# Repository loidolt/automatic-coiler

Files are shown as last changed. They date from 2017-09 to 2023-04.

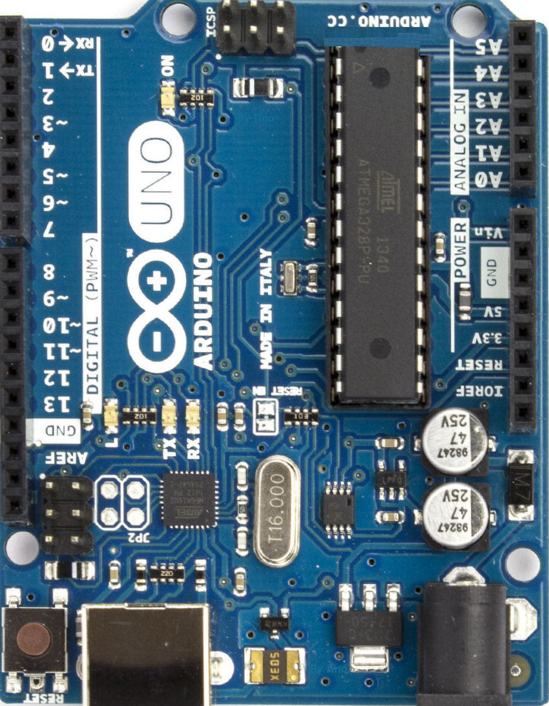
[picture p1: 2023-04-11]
V1/3d-model/AutomaticCoiler/ArduinoRev3CaraComponentes.jpg

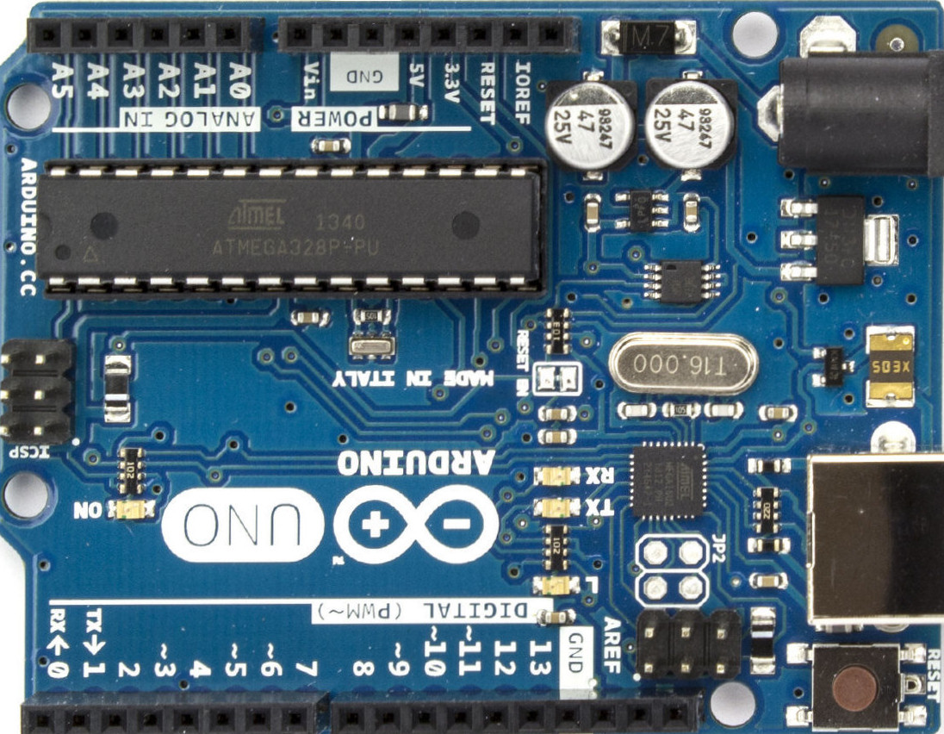
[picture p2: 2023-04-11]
V1/3d-model/AutomaticCoiler/CaraComponentes2.jpg

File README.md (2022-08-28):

---
published: true
status: complete
date: 10/26/2016
tags: 3DPrinting Electronics
description: An automatic winding machine for coiling up small cords, strings or wire.
slug: automatic-winding-machine
---

# Automatic Coiler

An automatic winding machine for coiling up small cords, strings or wire.

## Table of Contents

- [Automatic Coiler](#automatic-coiler)
  - [Table of Contents](#table-of-contents)
  - [Summary](#summary)
  - [Print Settings](#print-settings)
    - [Resolution:](#resolution)
    - [Infill:](#infill)
    - [Filament_material:](#filament_material)
    - [Notes:](#notes)
  - [Bill of Materials](#bill-of-materials)
    - [Hardware](#hardware)
      - [Tubing and Shafts:](#tubing-and-shafts)
      - [Bearings:](#bearings)
      - [Fasteners:](#fasteners)
      - [Other:](#other)
    - [Electronics](#electronics)
      - [Mechanical:](#mechanical)
      - [Control:](#control)

## Summary

This is an automatic winding machine for coiling up small cords, strings, or wires. We needed a way to reliably coil up specific lengths of cord for sale in a kit. This machine is the updated version of my original Automatic Winding Machine, making it more reliable, easier to use, and above all much, much quieter.

The rotary encoder keeps track of the distance coiled with a closed-loop system. This allows more foolproof operation, recovery if the spool hangs up or jams, and the ability to adjust the diameter of the coil without having to change the code.

This version features an LCD display with button controls, easy to edit firmware, more robust encoder guide system, an integrated spool holder, a quiet belt-driven platter, enclosed electronics, and a ton of other tiny tweaks and improvements.

Let me know if you have any questions or need build instructions. I'm happy to provide more detail but will need time to do the full instructional write-up. I can also provide pre-built custom acrylic panels and aluminum plates on request for a small fee.

Happy building!

## Print Settings

### Resolution:

.3

### Infill:

50

### Filament_material:

PLA or PETG

### Notes:

Print the Guide Wheels and Idler Wheel at high resolution, I used 0.1 mm layer height and 3 perimeters.

Print the Plate Shaft Mount solid (100% infill) to ensure it is nice and rigid.

## Bill of Materials

### Hardware

2020 Misumi T-Slot:

- 16x 260mm
- 4x 450mm

Lots of Cast Aluminum Corner Brackets (or print some if you want plastic brackets)

#### Tubing and Shafts:

- 1x 8mm x 75mm Round Metal Rod
- 2x 16mm OD x 215mm Round Aluminum Tube

#### Bearings:

18x 623Z Flange Bearing
2x 608Z

#### Fasteners:

- 4x M8-1.25 x 16mm Button Head Hex Socket Cap Screws
- A bunch of M4 screws, washers, and t-slot nuts

#### Other:

- M3 x 50mm Round Aluminum Standoff
- 1/4" x 12" Aluminum 5052 Plate Disk
- 2x 12"x12" White Acrylic Sheet

### Electronics

#### Mechanical:

- 1x Signswise 600p/r Incremental Rotary Encoder Dc5-24v Wide Voltage Power Supply 6mm Shaft
- 1x Greartisan DC 12V 200RPM Gear Motor High Torque
- 1x GT2 Pulley 20 Teeth 6mm Bore
- 1x GT2 Pulley 60 Teeth 8mm Bore
- 1x GT2 158mm Timing Belt Closed Loop
- 1x 10A 250V AC Inlet with Rocker Switch
- 1x Panel Mount USB Cable B to B

#### Control:

- 1x L298N Motor Drive
- 1x Arduino Nano
- 1x 16x2 LCD
- 2x 40mm Fan
- 1x 120v to 12v Power Supply (5-10 amp depending on your motor choice)
- 4x Arcade Buttons

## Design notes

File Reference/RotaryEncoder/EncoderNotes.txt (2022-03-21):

Encoders have an A and a B output. Tieing A to and interrupt pin and B to an input. On interrupt from A check B and if HIGH add 1 to PositionVar, if B is low Subtract 1 from PositionVar.

https://youtu.be/dTGITLnYAY0

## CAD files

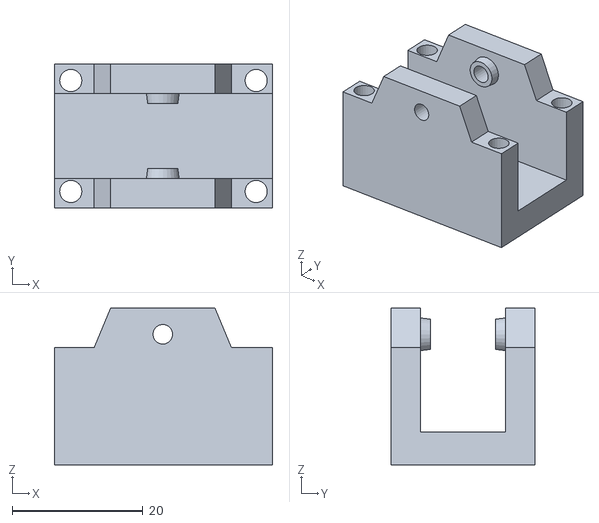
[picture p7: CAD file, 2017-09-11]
V1/stl/Encoder/EncoderIdlerAssembly.stl
33.4 x 22.0 x 24.0

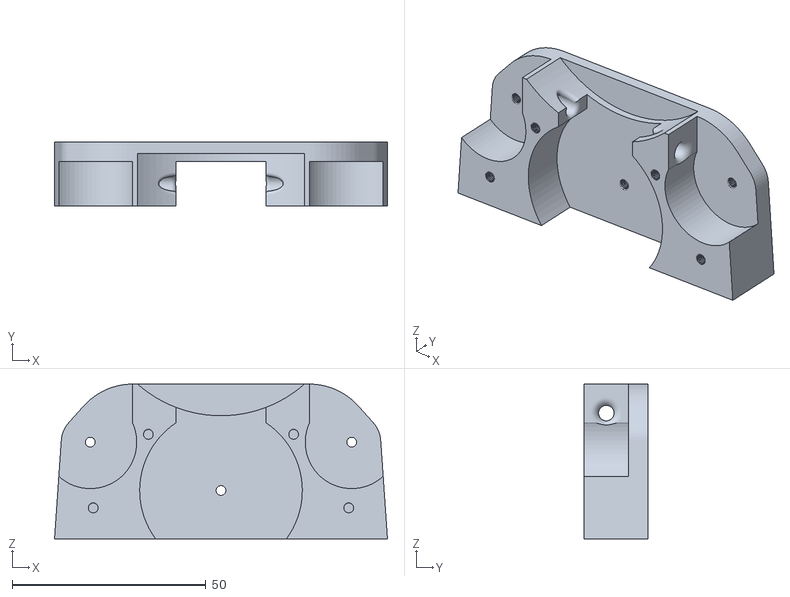
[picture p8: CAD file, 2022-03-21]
3d-model/stl/EncoderCordGuideMain.stl
86.0 x 16.5 x 40.0

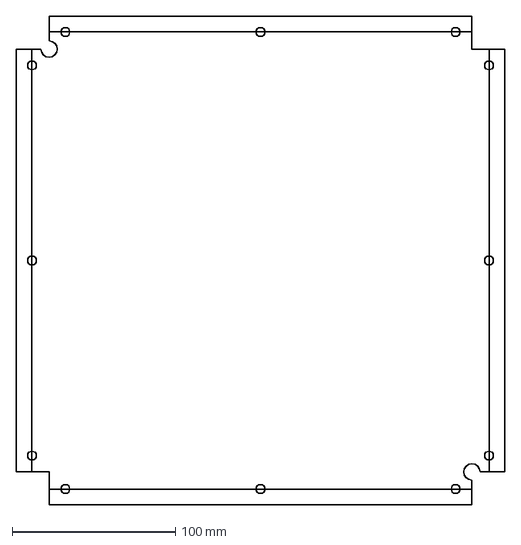
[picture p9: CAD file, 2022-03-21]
3d-model/ElectronicsCover.dxf
299.0 x 299.0 mm

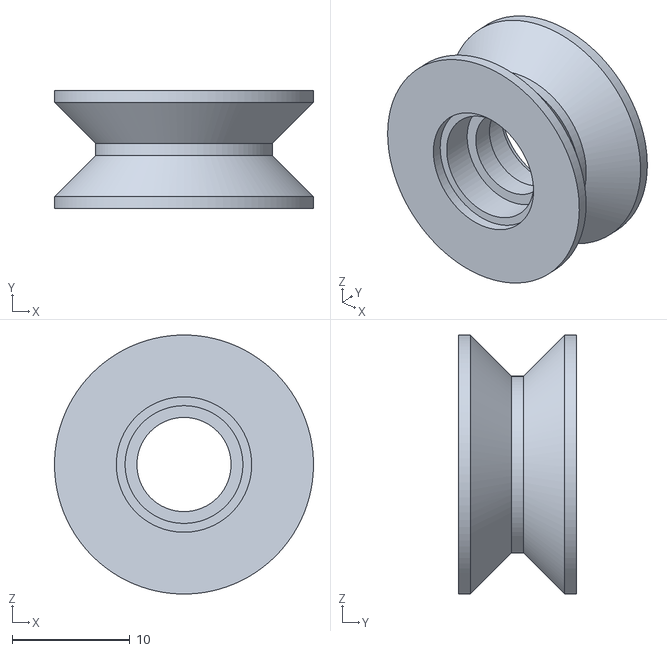
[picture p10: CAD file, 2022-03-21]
3d-model/stl/CordWheel.stl
22.0 x 10.0 x 22.0

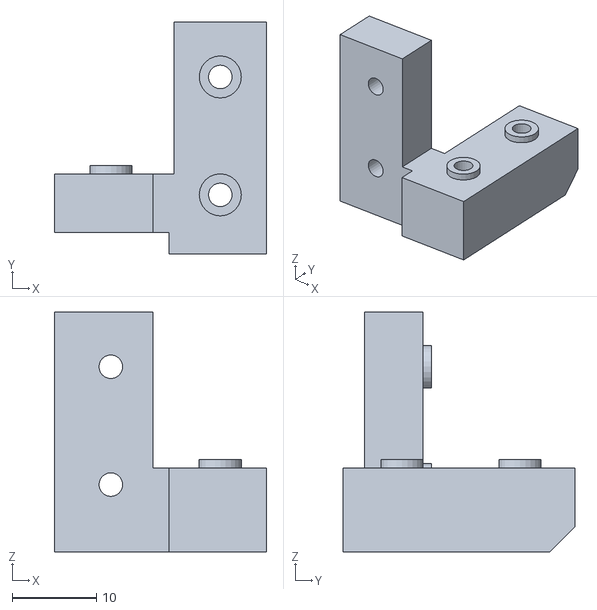
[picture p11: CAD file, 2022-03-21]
3d-model/stl/V2/CordGuideBearings.stl
25.2 x 27.5 x 28.5

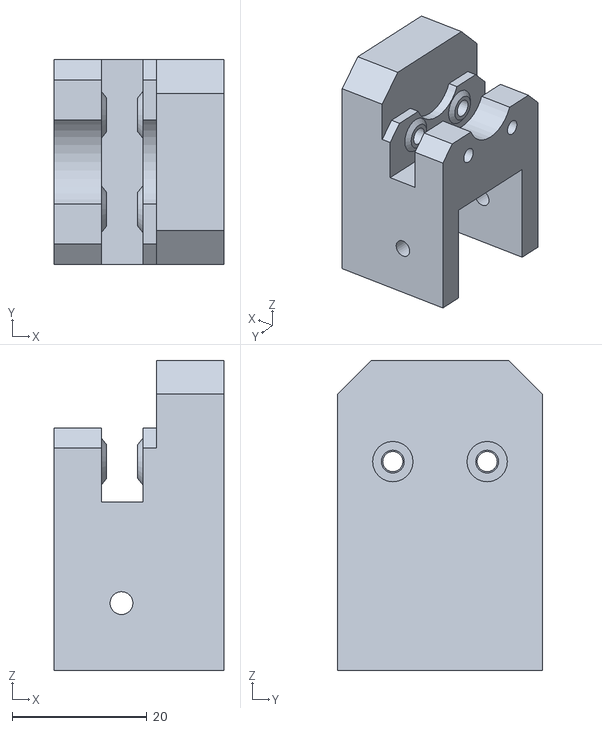
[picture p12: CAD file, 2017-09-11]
V1/3d-model/SpoolHolder/stl/BearingMount.stl
25.2 x 30.4 x 46.0

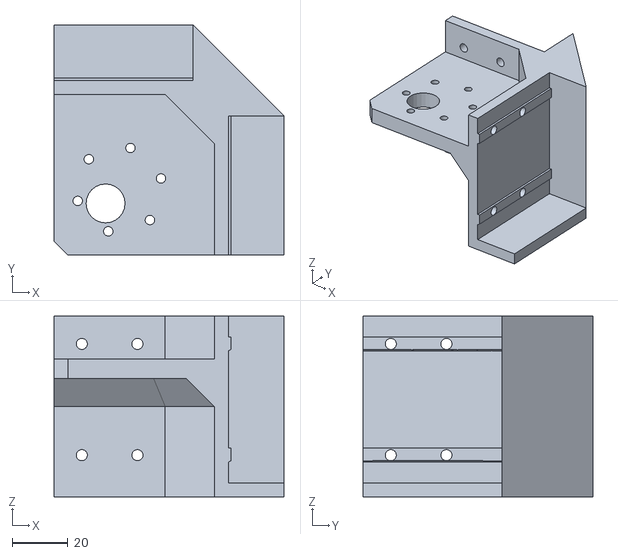
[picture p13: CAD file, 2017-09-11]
V1/stl/DCMotorCorner.stl
82.7 x 82.7 x 65.0

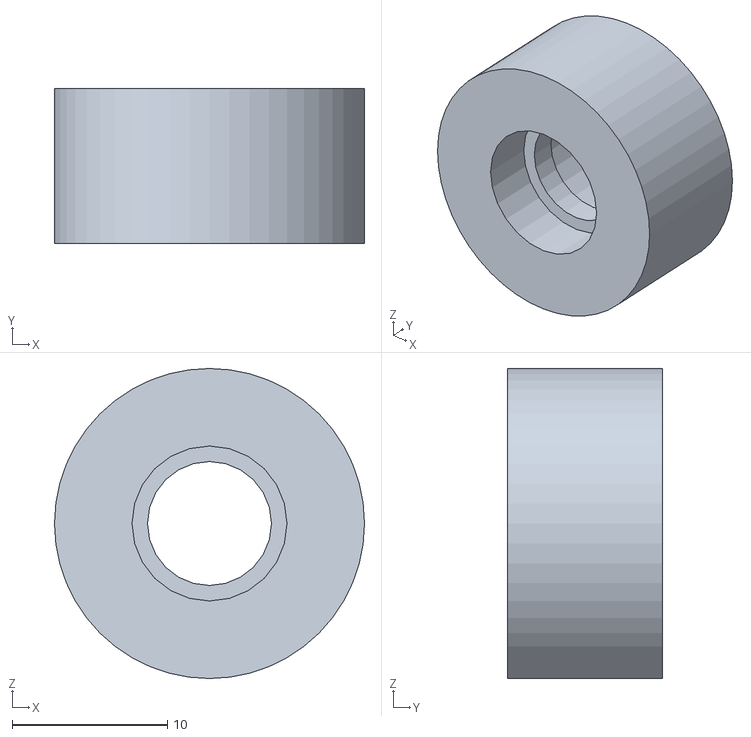
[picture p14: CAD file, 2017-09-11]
V1/stl/Encoder/IdlerWheel.stl
20.0 x 10.0 x 20.0

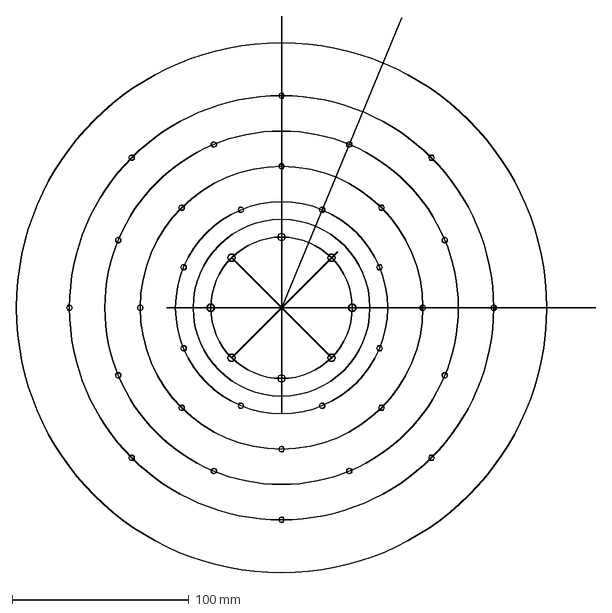
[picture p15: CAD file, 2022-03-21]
3d-model/PlateHolePattern.dxf
327.7 x 315.0 mm

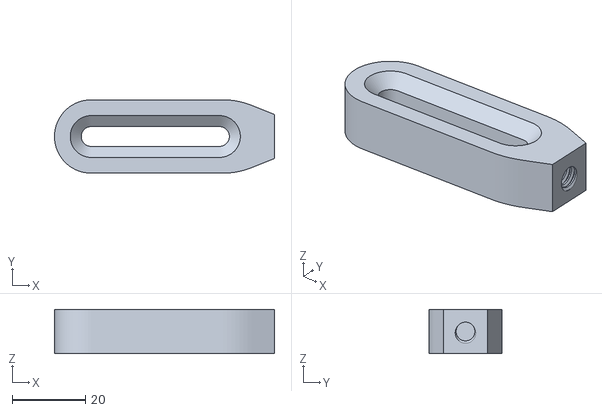
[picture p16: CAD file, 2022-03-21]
3d-model/stl/CenteringGuideArm.stl
60.0 x 20.0 x 12.0

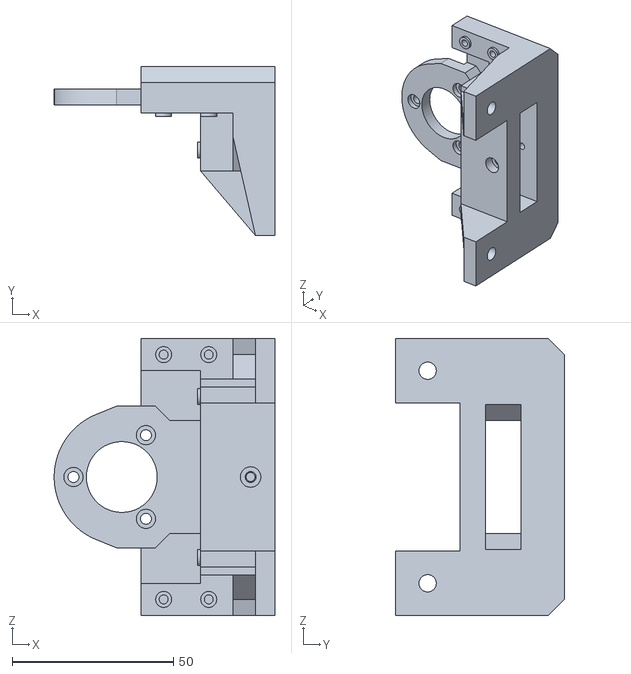
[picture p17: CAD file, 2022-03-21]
3d-model/stl/V2/EncoderHousing.stl
68.5 x 52.5 x 86.0

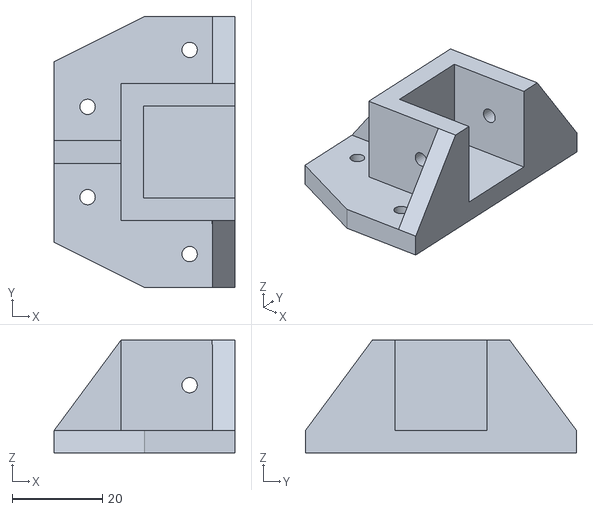
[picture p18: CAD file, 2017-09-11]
V1/3d-model/SpoolHolder/stl/90DegreeBracket.stl
40.0 x 60.0 x 25.0

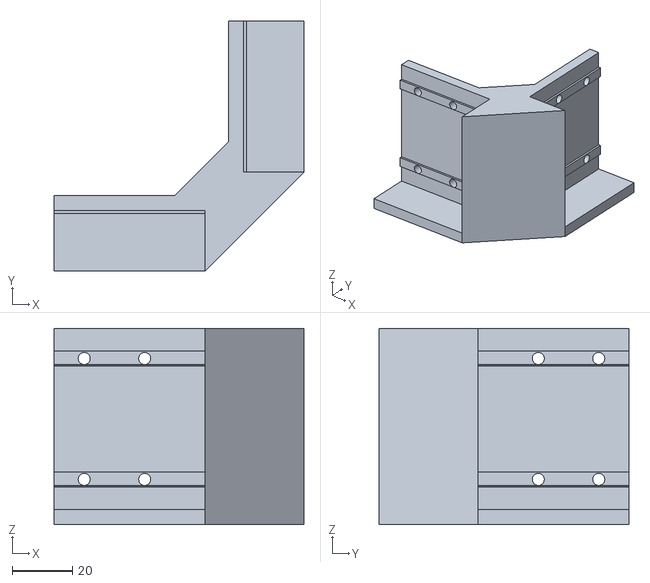
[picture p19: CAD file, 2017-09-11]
V1/stl/Corner.stl
82.7 x 82.7 x 65.0

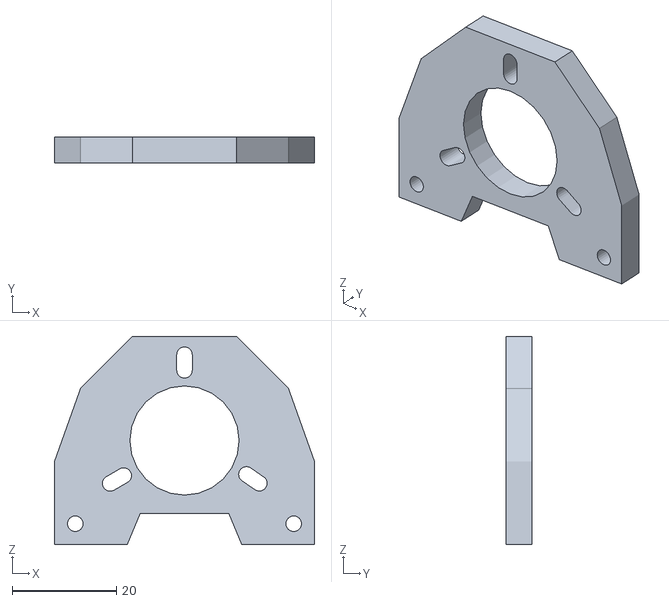
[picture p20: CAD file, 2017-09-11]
V1/stl/Encoder/EncoderMountPlate.stl
50.0 x 5.00 x 40.0

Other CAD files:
3d-model/stl/SidePanelACOutlet.stl
3d-model/stl/V2/SidePanelFan.stl
V1/3d-model/SpoolHolder/stl/Foot.stl
V1/stl/Encoder/EncoderHousing.stl
3d-model/stl/BearingBlock.stl
3d-model/stl/CenteringGuideMount.stl
3d-model/stl/ControlPanelLeft.stl
3d-model/stl/ControlPanelRight.stl
3d-model/stl/EncoderCordGuideCover.stl
3d-model/stl/GuideMount.stl
3d-model/stl/GuideWheelHolder.stl
3d-model/stl/GuideWheelHolderClamp.stl
3d-model/stl/IdlerWheel.stl
3d-model/stl/L298NMount.stl
3d-model/stl/MotorMount.stl
3d-model/stl/PCBMount.stl
3d-model/stl/PlateShaftMount.stl
3d-model/stl/RodHolderLeft.stl
3d-model/stl/RodHolderRight.stl
3d-model/stl/SidePanel.stl
3d-model/stl/SidePanelFan.stl
3d-model/stl/SidePanelVent.stl
3d-model/stl/SpoolHolder.stl
3d-model/stl/USBPanel.stl
3d-model/stl/V1.5/BearingToTubeCoupler.stl
3d-model/stl/V1.5/CordGuide.stl
3d-model/stl/V1.5/GuideClamp.stl
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

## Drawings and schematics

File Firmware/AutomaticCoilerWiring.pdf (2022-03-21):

## VCC VCC

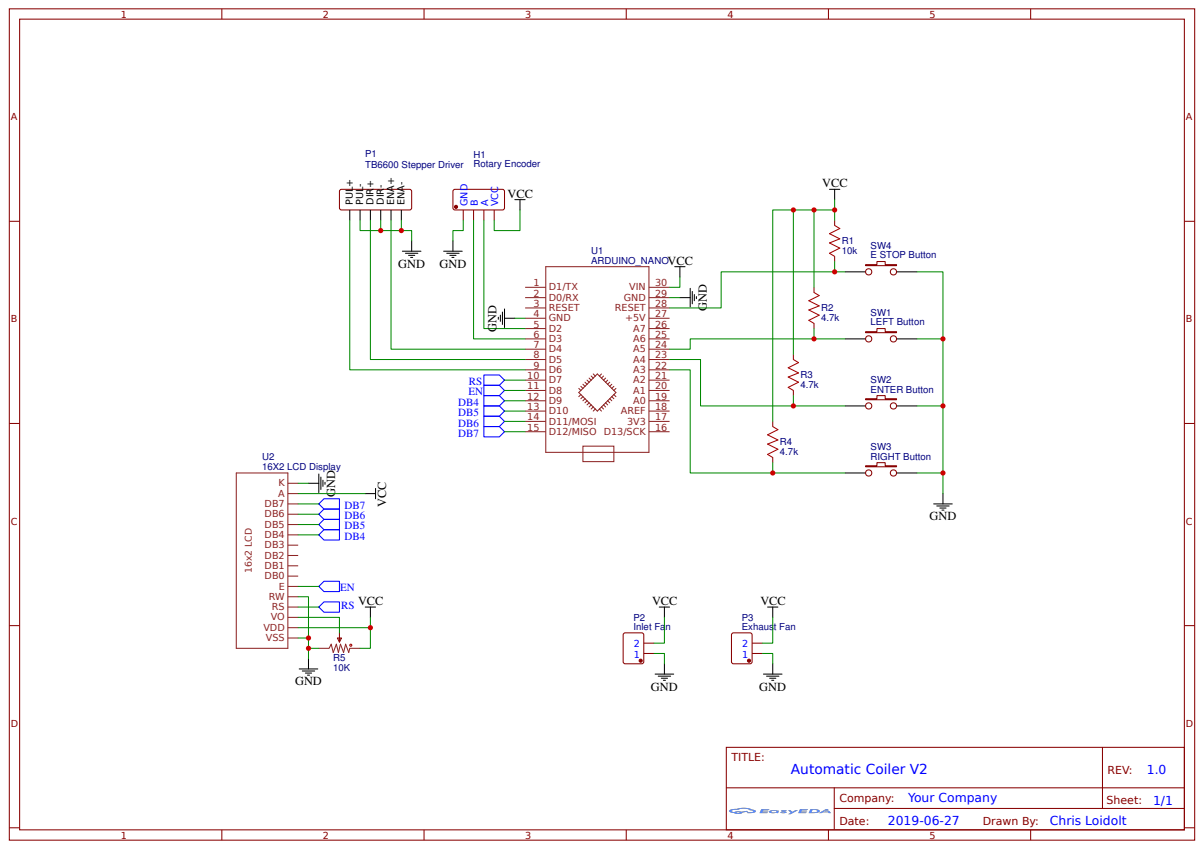
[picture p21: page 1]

Drawn By: Chris Loidolt

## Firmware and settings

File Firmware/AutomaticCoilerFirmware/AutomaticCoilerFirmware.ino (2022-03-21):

//Automatic Coiler V3
//Chris Loidolt
//03/15/2022

#include <LiquidCrystal.h>

//LCD
LiquidCrystal lcd(7, 8, 9, 10, 11, 12);
unsigned long previousMillis = 0; // will store last time LCD was updated
const long updateInterval = 200; // interval at which to update LCD while running job (milliseconds)

//Define Various Menu Variables used throughout
int timer = 0;
byte totalRows = 2;              // total rows of LCD
byte totalCols = 16;             // total columns of LCD
int returndata = 0;              // Used for return of button presses
unsigned long timeoutTime = 0;   // this is set and compared to millis to see when the user last did something.
const int menuTimeout = 20000;   // time to timeout in a menu when user doesn't do anything.
unsigned long lastButtonPressed; // this is when the last button was pressed. It's used to debounce.
const int debounceTime = 150;    // this is the debounce and hold delay. Otherwise, you will FLY through the menu by touching the button.

const int buttonUp = A5;     // Set pin for UP Button
const int buttonSelect = A4; // Set pin for SLELECT Button
const int buttonDown = A3;   // Set pin for DOWN Button

int buttonStateUp = 0; // Initalise ButtonStates
int buttonStateDown = 0;
int buttonState;

// constants for indicating whether cursor should be redrawn
#define MOVECURSOR 1
// constants for indicating whether cursor should be redrawn
#define MOVELIST 2

//Encoder
const int encoder_a = 2; // Green (Red - 5v, Black - GND)
const int encoder_b = 3; // White
long encoder = 0;
const float wheelPerimeter = 200; //mm
const int pulsesPerRev = 200;
float distancePerPulse;

//L298N Motor Driver
#define enA 6
#define in1 5
#define in2 4
int speedPWM = 0;
int minPWM = 120;

bool CWRotation = true;
int acceleration = 2;

//Job Variables
float feedLength = 0;
float distance = 0;
float overshootLength = 260; //Deceleration overshoot length offset

//Menu Variables
int menuItem = 0;

//Function Prototypes
void encoderPinChangeA(void);
void encoderPinChangeB(void);
int read_buttons();
void RunJob(void);
void calcDistance();
void EnterQty(void);

//Preset Lengths (inches)
const int guylineCordLength = 1200;
const int ridgelineLength = 300;

void setup()
{

  // set up the LCD's number of columns and rows:
  lcd.begin(totalCols, totalRows);

  // initialize the serial communications port:
  Serial.begin(9600);

  pinMode(buttonUp, INPUT);
  pinMode(buttonDown, INPUT);
  pinMode(buttonSelect, INPUT);

  // Encoder Setup
  pinMode(encoder_a, INPUT_PULLUP);
  pinMode(encoder_b, INPUT_PULLUP);
  
  attachInterrupt(0, encoderPinChangeA, RISING);
  
  //Calculate encoder distance per pulse
  distancePerPulse = wheelPerimeter / pulsesPerRev;

  //Motor Setup
  pinMode(enA, OUTPUT);
  pinMode(in1, OUTPUT);
  pinMode(in2, OUTPUT);
  // Set initial rotation direction
  digitalWrite(in1, LOW);
  digitalWrite(in2, HIGH);

  speedPWM = minPWM;

  // Boot Up Message
  Serial.println("Automatic Coiler");
  lcd.print("Automatic Coiler");
  lcd.setCursor(0, 1);
  lcd.print("Starting Up");
  Serial.print("Starting Up");
  delay(300);
  for (int i = 0; i < 6; i++)
  {
    Serial.print(".");
    lcd.print(".");
    delay(100);
  }

  Serial.begin(9600);

  lcd.clear();

  displayMenu();
}

void calcDistance()
{
  //Convert mm to inches
  distance = (encoder * distancePerPulse) / 25.4;
  Serial.println(distance);
}

void RunJob(int feedLength)
{
  //Set Motor Direction Forward
  digitalWrite(in1, HIGH);
  digitalWrite(in2, LOW);
  delay(20);
        
  int accelerationDistance = 0;

  lcd.setCursor(0, 1);
  lcd.print("                ");
  lcd.setCursor(7, 1);
  lcd.print("/");
  lcd.print(feedLength);
  lcd.print("in");

  //Smooth Start
  while (speedPWM < 255) {

    calcDistance();
    
    Serial.print(distance);
    Serial.print("/");
    Serial.println(feedLength);

    unsigned long currentMillis = millis();

    if (currentMillis - previousMillis >= updateInterval) {
      // save the last time we updated LCD
      previousMillis = currentMillis;
  
      lcd.setCursor(0, 1);
      lcd.print("       ");
      lcd.setCursor(0, 1);
      lcd.print((int)distance);
    }
    
    analogWrite(enA, speedPWM); // Send PWM signal to L298N Enable pin
    speedPWM = speedPWM + acceleration;
    delay(100);
    accelerationDistance = distance;
  }

  //Run Full Speed
  while (distance < feedLength - accelerationDistance - overshootLength) {

    calcDistance();
    
    Serial.print(distance);
    Serial.print("/");
    Serial.println(feedLength);
    
    unsigned long currentMillis = millis();

    if (currentMillis - previousMillis >= updateInterval) {
      // save the last time we updated LCD
      previousMillis = currentMillis;
  
      lcd.setCursor(0, 1);
      lcd.print("       ");
      lcd.setCursor(0, 1);
      lcd.print((int)distance);
    }

    analogWrite(enA, 255); // Send PWM signal to L298N Enable pin

    
  }

  //Decelerate
  while (speedPWM > minPWM) {

    calcDistance();
    
    Serial.print(distance);
    Serial.print("/");
    Serial.println(feedLength);
    
    unsigned long currentMillis = millis();

    if (currentMillis - previousMillis >= updateInterval) {
      // save the last time we updated LCD
      previousMillis = currentMillis;
  
      lcd.setCursor(0, 1);
      lcd.print("       ");
      lcd.setCursor(0, 1);
      lcd.print((int)distance);
    }
    
    analogWrite(enA, speedPWM); // Send PWM signal to L298N Enable pin
    speedPWM = speedPWM - acceleration;
    delay(100);
  }

  //Fine Tune Length
  while (distance < feedLength) {

    calcDistance();
    
    Serial.print(distance);
    Serial.print("/");
    Serial.println(feedLength);
    
    unsigned long currentMillis = millis();

    if (currentMillis - previousMillis >= updateInterval) {
      // save the last time we updated LCD
      previousMillis = currentMillis;
  
      lcd.setCursor(0, 1);
      lcd.print("       ");
      lcd.setCursor(0, 1);
      lcd.print((int)distance);
    }

    analogWrite(enA, minPWM); // Send PWM signal to L298N Enable pin

    
  }
  
  analogWrite(enA, 0); // Send PWM signal to L298N Enable pin

  speedPWM = minPWM;
  encoder = 0; //empty for next round
  distance = 0; //empty for next round

  Serial.println("Done!");

  lcd.setCursor(0, 1);
  lcd.print("                ");
  lcd.setCursor(0, 1);
  lcd.print("Done!");

  delay(1000);

  displayMenu();
}

void displayMenu(){
  switch (menuItem) {
    case 0:
      Serial.println("Guyline Cord");
      lcd.clear();
      lcd.setCursor(0, 0);
      lcd.print("Guyline Cord");
      lcd.setCursor(0, 1);
      lcd.print("1200in, 1.5mm YL");
      break;

    case 1:
      Serial.println("Ridgeline Cord");
      lcd.clear();
      lcd.setCursor(0, 0);
      lcd.print("Ridgeline Cord");
      lcd.setCursor(0, 1);
      lcd.print("300in, 1.5mm GR");
      break;

    case 2:
      Serial.println("Reset Distance");
      lcd.clear();
      lcd.setCursor(0, 0);
      lcd.print("Reset Distance");
      break;

    case 3:
      Serial.println("Reverse Motor");
      lcd.clear();
      lcd.setCursor(0, 0);
      lcd.print("Reverse Motor");
      lcd.setCursor(0, 1);
      lcd.print("2 seconds");
      break;
  }
}

void loop()
{

  switch (read_buttons()){
    case 1: //Left Button Pushed
      if (menuItem > 0) {
        menuItem = menuItem - 1;
        displayMenu();
      }
      break;

    case 2: //Right Button Pushed
      if (menuItem < 4) {
        menuItem = menuItem + 1;
        displayMenu();
      }
      break;

    case 3: //Enter Button Pushed
    
      switch (menuItem){
        case 0: // menu item 1 selected
          Serial.println("Guyline Cord");
          lcd.clear();
          lcd.setCursor(0, 0);
          lcd.print("Guyline Cord");
          RunJob(guylineCordLength);
          break;

        case 1: // menu item 2 selected
          Serial.println("Ridgeline");
          lcd.clear();
          lcd.setCursor(0, 0);
          lcd.print("Ridgeline");
          RunJob(ridgelineLength);
          break;
  
        case 2: // menu item 3 selected
          Serial.println("Counter Reset");
          lcd.clear();
          lcd.setCursor(0, 0);
          lcd.print("Counter Reset!");
          encoder = 0;
          delay(2000);
          displayMenu();
          break;
        
        case 3: // menu item 4 selected
          Serial.println("Reverse");
          lcd.clear();
          lcd.setCursor(0, 0);
          lcd.print("Reversing");
          encoder = 0;
          digitalWrite(in1, LOW);
          digitalWrite(in2, HIGH);
          delay(20);
          analogWrite(enA, 180); // Send PWM signal to L298N Enable pin
          delay(2000);
          analogWrite(enA, 0); // Send PWM signal to L298N Enable pin
          digitalWrite(in1, HIGH);
          digitalWrite(in2, LOW);
          delay(20);
          displayMenu();
          break;
      }
      
      break;
  }
}

int read_buttons()
{ // you may need to swap "void" with "int" or "byte"

  int returndata = 0;

  if ((lastButtonPressed + debounceTime) < millis())
  { // see if it's time to check the buttons again

    // read Up button
    buttonState = digitalRead(buttonUp);

    if (buttonState == LOW)
    {
      returndata = 1;
      lastButtonPressed = millis();
      Serial.println("UP");
    }

    // read Down button
    buttonState = digitalRead(buttonDown);

    if (buttonState == LOW)
    {
      returndata = 2;
      lastButtonPressed = millis();
      Serial.println("DOWN");
    }

    //read Select button
    buttonState = digitalRead(buttonSelect);

    if (buttonState == LOW)
    {
      returndata = 3;
      lastButtonPressed = millis();
      Serial.println("SELECT");
    }
  }

  return returndata; // this spits back to the function that calls it the variable returndata.
}

void encoderPinChangeA() {
  if(digitalRead(encoder_b) == LOW) {
    encoder++;
  } else{
    encoder--;
  }
}

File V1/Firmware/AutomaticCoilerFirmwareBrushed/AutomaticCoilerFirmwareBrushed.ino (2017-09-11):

/****************************************************************************** 
Automatic Coiler Firmware V1
******************************************************************************/
#include <LiquidCrystal.h>

int motor = 2;

//Encoder Pins
// Red - 5V
// Black - GND
const int encoder_a = 4; // Green - pin 2 - Digital
const int encoder_b = 3; // White - pin 3 - Digital
long encoder = 0;

//Buttons
int enter = A1;
int back = A2;
int next = A3;

//Set Distances
int guyline = 80;


//Variables
int user_input;
int distance;
int x;
char c;
int count;

LiquidCrystal lcd(5, 6, 10, 9, 8, 7);

void setup(){
  /*Sets all pin to output; the microcontroller will send them(the pins) bits, it will not expect to receive any bits from thiese pins.*/
  pinMode(motor, OUTPUT);

  pinMode(encoder_a, INPUT_PULLUP);
  pinMode(encoder_b, INPUT_PULLUP);

  attachInterrupt(0, encoderPinChangeA, CHANGE);
  attachInterrupt(1, encoderPinChangeB, CHANGE);

  pinMode(enter, INPUT_PULLUP);
  pinMode(back, INPUT_PULLUP);
  pinMode(next, INPUT_PULLUP);

  lcd.begin(16,2);
 
  Serial.begin(9600); 

   //Print function list for user selection
  Serial.println("Choose Option:");
  Serial.println();
  lcd.print("Enter length");
}
 
void loop(){
  
  while(Serial.available()){
      user_input = Serial.parseInt(); //read int or parseFloat for ..float...
      
      Serial.println(user_input);
      Serial.println();
      
      if (user_input = 1)
      { 
        CustomLength();
      }
      else if (user_input = 2)
      {
        GuyLine();
      }
      else
      {
        Serial.println("Invalid Number");
      }
  }
}

void CustomLength()
{ 
  Serial.println("Enter length:");
  Serial.println();
  lcd.print("Enter length");

  while(Serial.available()){
      user_input = 0; //empty for next input
      
      user_input = Serial.parseInt(); //read int or parseFloat for ..float...
      
      Serial.println(user_input);
      Serial.println();

      if (user_input >= 1)
      {
        user_input = 0; //empty for next input
        
        user_input = Serial.parseInt(); //read int or parseFloat for ..float...
      
        Serial.println(user_input);
        Serial.println();
        
        Serial.print("Winding ");
        Serial.print(user_input);
        Serial.println(" in");
        Serial.println();
        lcd.clear();
        lcd.print("Winding ");
        lcd.print(user_input);
        lcd.print(" in");
  
        while(distance < user_input)
        {
          digitalWrite(motor, HIGH);
          distance = encoder / 600;
        }
  
        digitalWrite(motor, LOW);

        user_input = 0; //empty for next input
        encoder = 0; //empty for next round
        distance = 0; //empty for next round
        Serial.println("Enter new distance");
        Serial.println();
        lcd.clear();
        lcd.print("Enter next");
      }
      else
      {
        Serial.println("Invalid Number");
      }
  }
}

void GuyLine()
{ 
  Serial.print("Coiling guyline cord section");
  Serial.println();
  
  while(distance < guyline)  //Loop the forward stepping until set cord is coiled
  {
    digitalWrite(motor, HIGH);  
    distance = encoder / 600;
  }
  
  digitalWrite(motor, LOW);

  user_input = 0; //empty for next input
  encoder = 0; //empty for next round
  distance = 0; //empty for next round
  Serial.println("Done");
  Serial.println();
}

void encoderPinChangeA() {
encoder += digitalRead(encoder_a) == digitalRead(encoder_b) ? -1 : 1;
}

void encoderPinChangeB() {
encoder += digitalRead(encoder_a) != digitalRead(encoder_b) ? -1 : 1;
}

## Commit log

2022-03-21 Fix folder names
    [BearingToTubeCoupler.stl, CordGuide.stl, GuideClamp.stl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]
2022-08-28 Re-structure repo
    [BearingBlock.stl, BearingToTubeCoupler.stl, CenteringGuideArm.stl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]
2023-04-11 Add additional model types
    [90DegreeBracket.stl, BearingMount.stl, CoilerSpoolHolder.skp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]
